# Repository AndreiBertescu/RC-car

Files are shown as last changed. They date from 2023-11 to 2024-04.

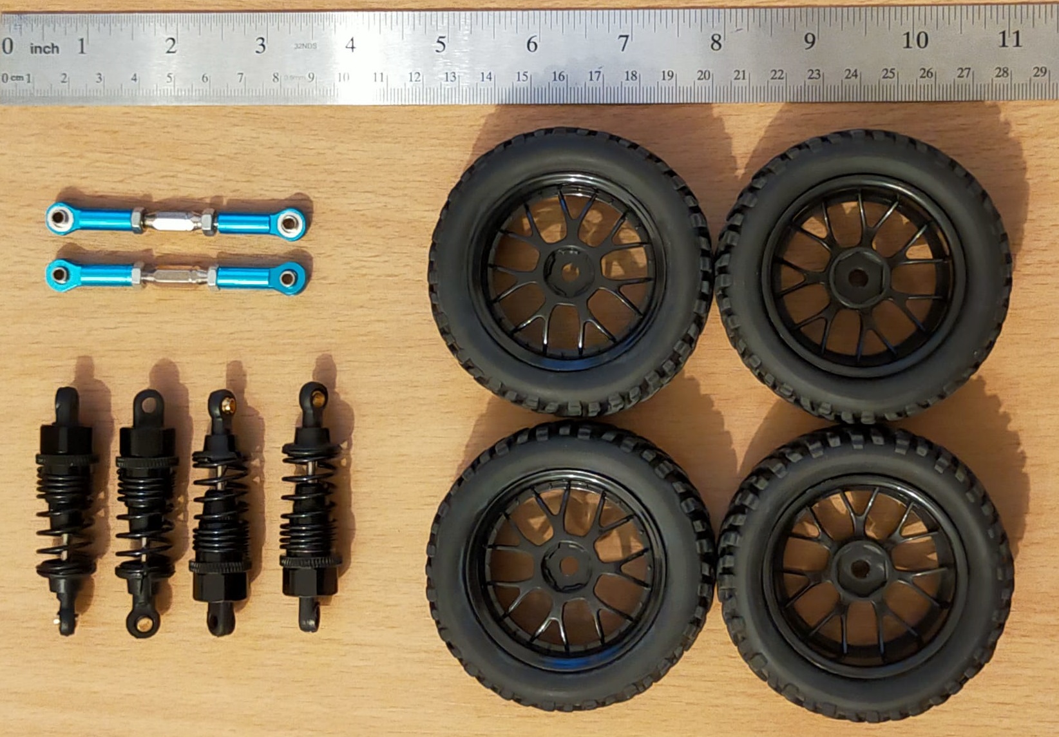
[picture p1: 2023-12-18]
Photos/Parts.jpg

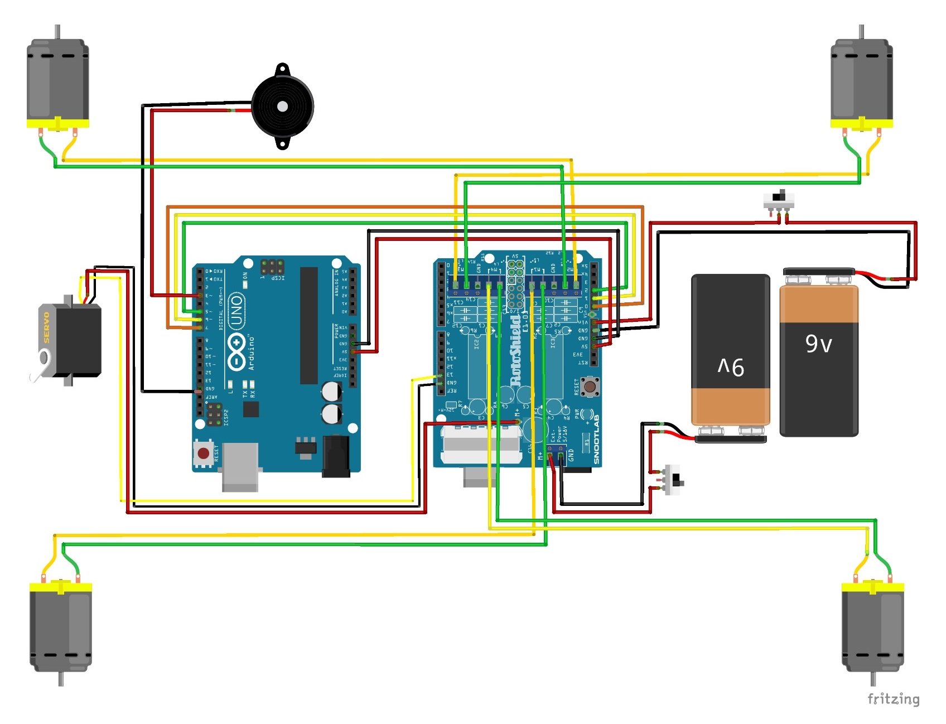
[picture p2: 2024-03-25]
Photos/Schematic.jpg

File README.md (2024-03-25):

# RC Car Project

This project aims to create an Arduino-controlled RC car.

<p align="center">
  
  
  
  
</p>

## Description

The setup includes a Plusivo Arduino Uno, paired with an Arduino WiFi board, and a quad H-bridge motor controller. To control the car, the WiFi board initiates a server, a WiFi access point and starts a RC-car-control web page. The car can be controlled from any device using the site's graphical user interface or by connecting any controller supported by the browser.

Two Arduino boards are used because the WiFi board lacks access to the OCR2A/B and OCR0A/B timers, while the Arduino Uno lacks built-in WiFi capability.

The car's chassis was designed in Fusion360 and will be 3D printed using PLA filament, while the wheels, suspensions, motors, battery, and wires are purchased separately. The car can work in two modes: one where the servo is not used to steer the car, only the wheels, and one where the servo is connected to the two steering axles, thus turning the wheels. In the former working mode, two stoppers have been designed to prevent the wheels from spinning on their own.

## Components
- 1x Arduino UNO R3 board: [datasheet](https://docs.arduino.cc/resources/datasheets/A000066-datasheet.pdf)
- 1x WEMOS ESP8266 D1 R2 board: [details](https://wiki.geekworm.com/WEMOS_ESP8266_D1_R2_V2.1)
- 1x L293D quad H-bridge motor controller shield: [manual](https://cdn-learn.adafruit.com/downloads/pdf/adafruit-motor-shield.pdf)
- 1x passive buzzer
- 4x 7.5cm diameter wheels.
- 4x 6cm hole-to-hole suspensions.
- 2x 6.5cm hole-to-hole steering axels (which have been extended).
- 1x MG996R 10Kg/cm servo motor for the steering arrangement.
- 2x 9V battery (which can be replaced with any rechargeable battery) - one for the motors and one for the control boards.
- A bunch of wires.
- Acces to a 3D-printer for the chassis.
- 
### Screws
- 8 x M3x20
- 20 x M4x15
- 12 x M4x40
- 16 x M5x30
- 16 x M5x40

## Controls for an Xbox controller
- Right joystick for steering
- Light joystick for speed
- Y button for START/STOP button
- B button for honk
- A button for steering lock

## Notes
- The joystick in the rc-car-control web page was made with the help of this tutorial: [link](https://www.instructables.com/Making-a-Joystick-With-HTML-pure-JavaScript/)
- The 'ArduinoWifiDriver' directory was included because of a recurring error when trying to write the program on the D1 R2 board.
- The website url to control the car is: http://192.168.4.1
- The website will load only if you are connected to the propper wifi network named '**RC-CAR_ESP8266**' with the password '**password**'.
- The Wheel-Connector model was not utilized. Instead, 4x M4x15 screws with a 2mm hole drilled in their center were used to connect the motors with the wheels.

## Version 1.4
- Added schematic
- Added passive buzzer with honk feature
- Added custom paintjob

## Version 1.3
- Updated chassis models with two available extensions: one specific to Fusion360 and stl.
- The total amount of filament used is 123 meters.

## Version 1.2
- Rechecked the Arduino Uno code to ensure it works
- Updated the README to include the schematic and part names

## Version 1.1
- Remade website to be more responsive
- Remade ArduinoWifi code to be more readable
- Removed the ability of the Arduino to connect to other wifi networks for simplicity

## Version 1.0
- Added project to GitHub

## Images
- Schematic
Schematic

- Car model


- Bought parts


- L293D motor controller


- WEMOS ESP8266 D1 R2


- Arduino UNO R3


- Front wheels assembly


- Small car components prepared for 3d-printing


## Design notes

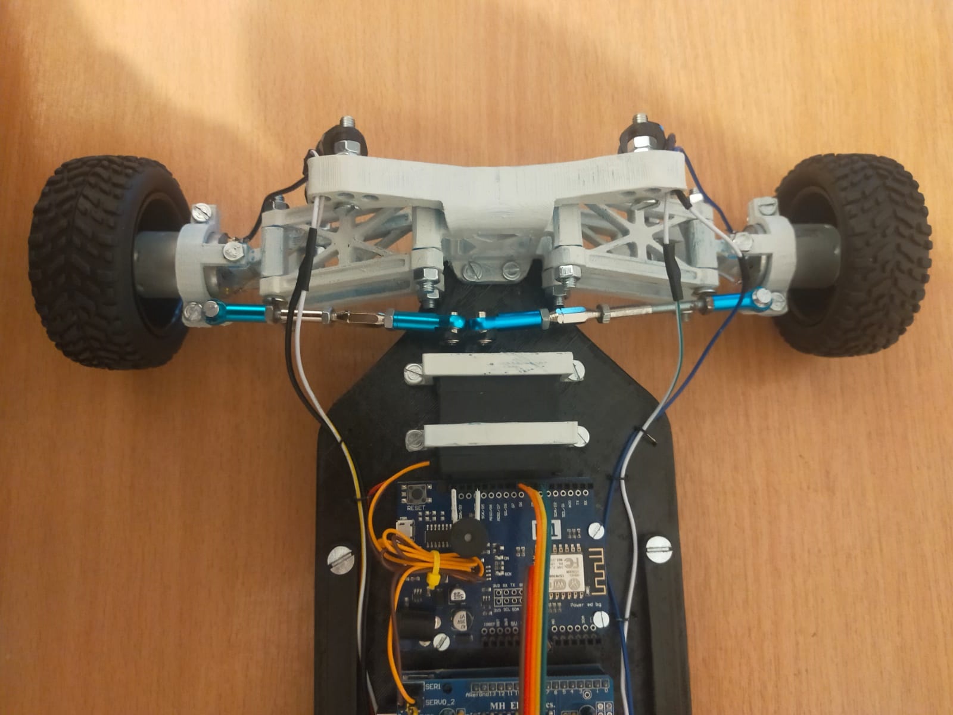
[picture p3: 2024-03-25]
Photos/Car1.jpg

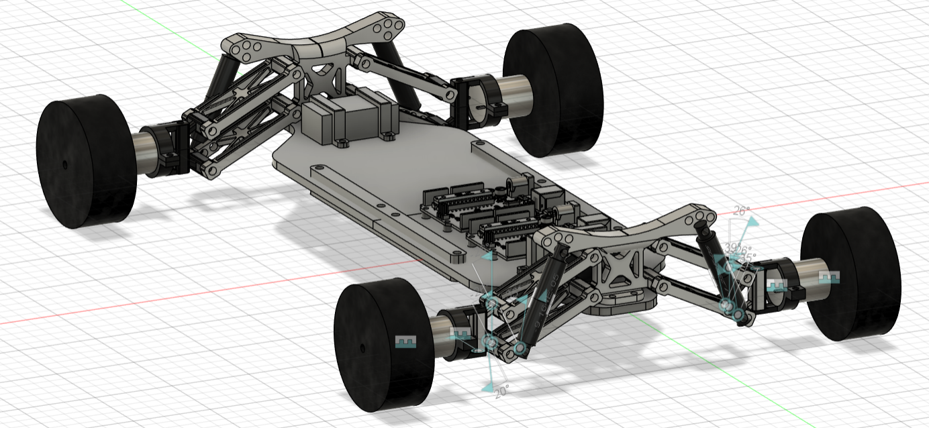
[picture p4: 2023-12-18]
Photos/Model3.png

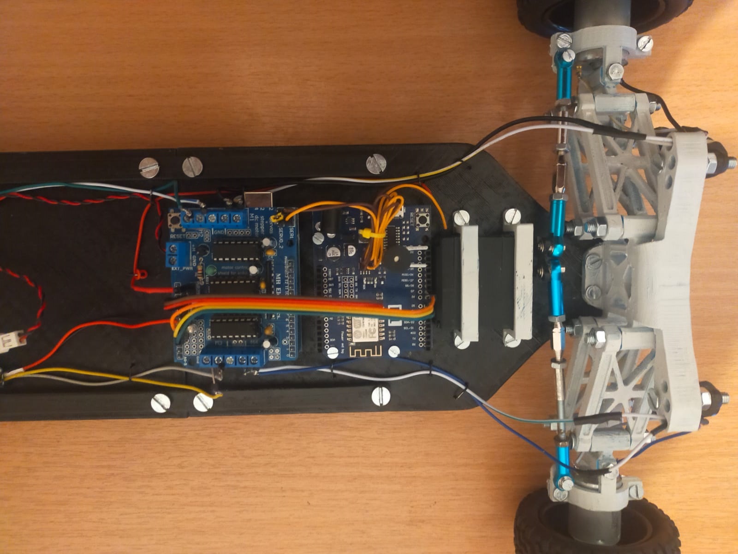
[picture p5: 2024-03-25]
Photos/Car4.jpg

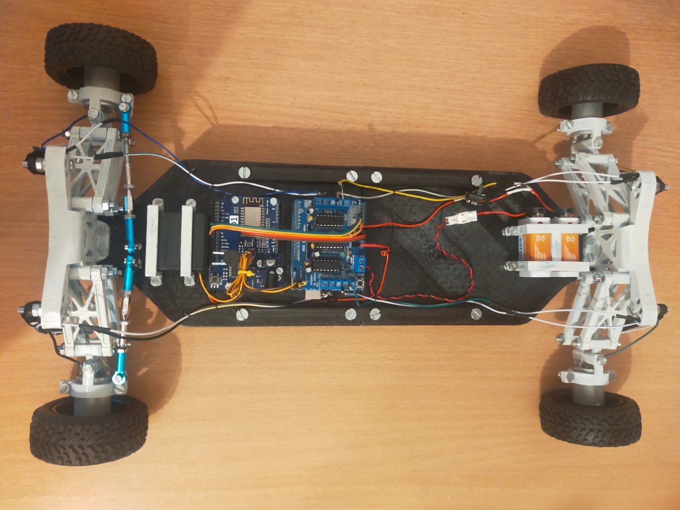
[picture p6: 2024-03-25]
Photos/Car2.jpg

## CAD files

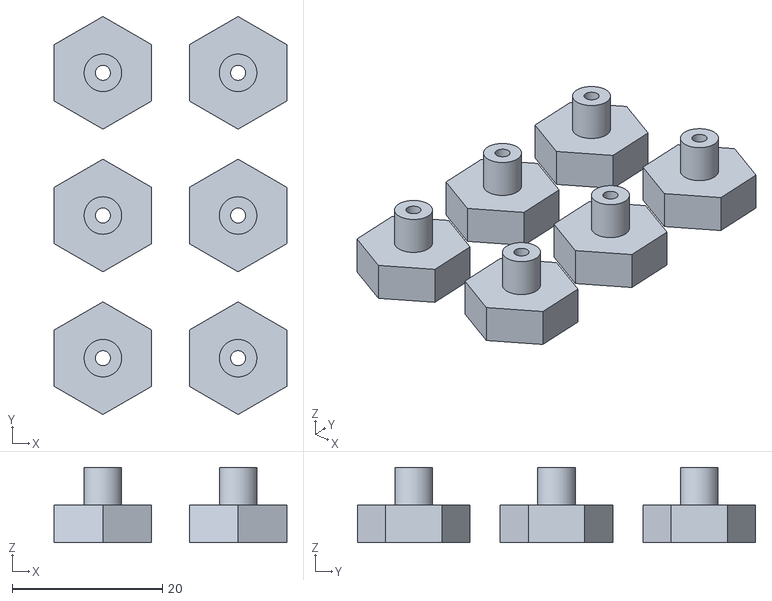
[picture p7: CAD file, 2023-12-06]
Model/Wheeel-Connectors.stl
31.0 x 53.0 x 10.0

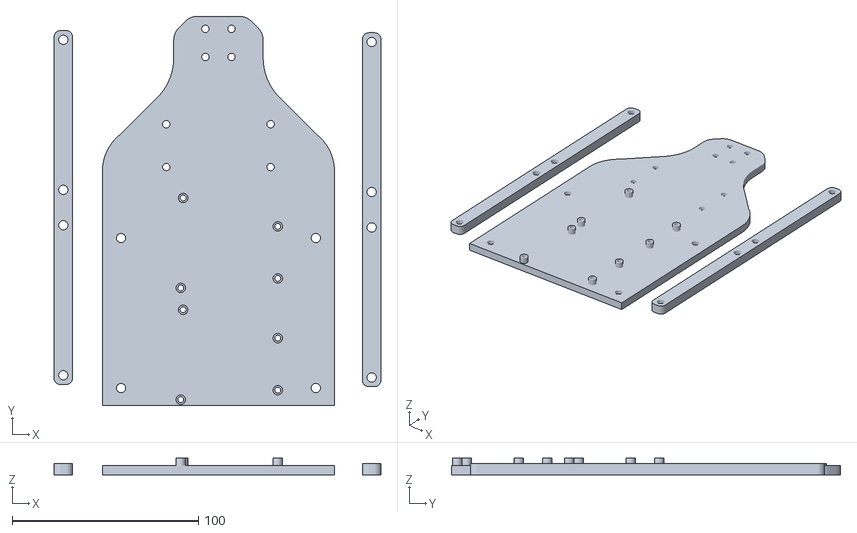
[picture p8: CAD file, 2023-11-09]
Model/3D-Plate1.stl
175.5 x 209.0 x 9.00

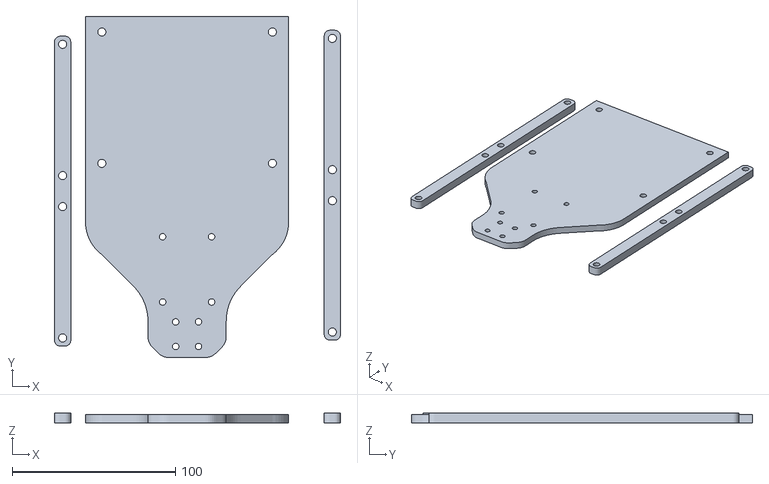
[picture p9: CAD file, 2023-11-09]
Model/3D-Plate2.stl
175.3 x 209.0 x 6.00

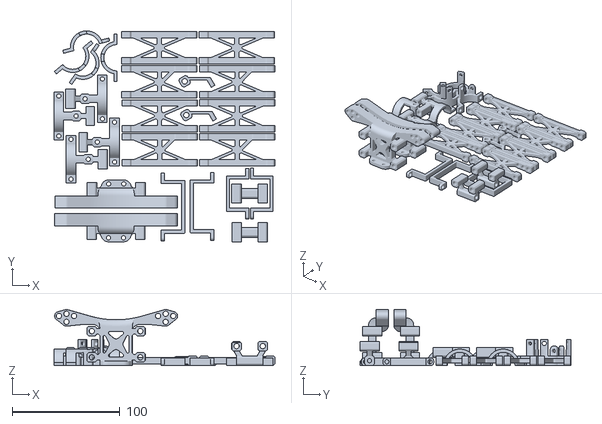
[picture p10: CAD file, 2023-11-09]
Model/3D-Components.stl
205.0 x 196.0 x 52.0

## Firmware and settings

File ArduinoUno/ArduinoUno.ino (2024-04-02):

#include <AFMotor.h>
#include <Servo.h>

AF_DCMotor motorForwardRight(2);
AF_DCMotor motorForwardLeft(3);
AF_DCMotor motorBackRight(1);
AF_DCMotor motorBackLeft(4);
int speed = 0;
int steering = 0;
bool steeringEnabled = 0;  //true when the servo is used

Servo steeringSero;  // create servo object to control a servo
int servoPos = 0;

//////////////////////SETTINGS
#define SPEED_PIN A2            //speed analog pin
#define STEERING_PIN A1         //steering analog pin
#define STEERING_ENABLE_PIN A0  //steering lock analog/digital pin
void setup() {
  Serial.begin(9600);

  pinMode(SPEED_PIN, INPUT);
  pinMode(STEERING_PIN, INPUT);
  pinMode(STEERING_ENABLE_PIN, INPUT);

  steeringSero.attach(10);
}

void loop() {
  retrieveValues();
  handleMotors();

  printValues();
  // printValueTimings();
}

void printValues() {
  Serial.print(speed);
  Serial.print(" ");
  Serial.print(steering);
  Serial.print(" ");
  Serial.print(steeringEnabled);
  Serial.println();
  delay(100);
}

void printValueTimings() {
  Serial.print(pulseIn(SPEED_PIN, HIGH, 980000));
  Serial.print(" ");
  Serial.print(pulseIn(STEERING_PIN, HIGH, 980000));
  Serial.print(" ");
  Serial.print(digitalRead(STEERING_ENABLE_PIN));
  Serial.println();
  delay(100);
}

void retrieveValues() {
  speed = map(pulseIn(SPEED_PIN, HIGH, 980000), 20, 975, -255, 255);
  steering = map(pulseIn(STEERING_PIN, HIGH, 980000), 20, 975, -255, 255);
  speed = (abs(speed) < 1 || abs(speed) >= 256) ? 0 : speed / 10 * 10;
  steering = (abs(steering) < 1 || abs(steering) >= 256) ? 0 : steering / 10 * 10;
  steeringEnabled = digitalRead(STEERING_ENABLE_PIN);
}

void handleMotors() {
  motorForwardRight.setSpeed(abs(speed));
  motorForwardLeft.setSpeed(abs(speed));
  motorBackRight.setSpeed(abs(speed));
  motorBackLeft.setSpeed(abs(speed));

  if (abs(speed) < 100) {
    motorForwardRight.run(RELEASE);
    motorForwardLeft.run(RELEASE);
    motorBackRight.run(RELEASE);
    motorBackLeft.run(RELEASE);
  } else if (speed >= 100) {
    motorForwardRight.run(FORWARD);
    motorForwardLeft.run(FORWARD);
    motorBackRight.run(FORWARD);
    motorBackLeft.run(FORWARD);
  } else if (speed <= -100) {
    motorForwardRight.run(BACKWARD);
    motorForwardLeft.run(BACKWARD);
    motorBackRight.run(BACKWARD);
    motorBackLeft.run(BACKWARD);
  }

  if (steeringEnabled) {
    if (abs(steering) > 50)
      steeringSero.write(map(steering, -255, 255, 135, 45));
    else
      steeringSero.write(90);
  } else if(abs(steering) > 100 && abs(speed) < 100){
    motorForwardRight.setSpeed(abs(steering));
    motorForwardLeft.setSpeed(abs(steering));
    motorBackRight.setSpeed(abs(steering));
    motorBackLeft.setSpeed(abs(steering));

    if (steering <= -100) {
      motorForwardRight.run(BACKWARD);
      motorForwardLeft.run(FORWARD);
      motorBackRight.run(BACKWARD);
      motorBackLeft.run(FORWARD);
    } else if (steering >= 100) {
      motorForwardRight.run(FORWARD);
      motorForwardLeft.run(BACKWARD);
      motorBackRight.run(FORWARD);
      motorBackLeft.run(BACKWARD);
    }
  }
}

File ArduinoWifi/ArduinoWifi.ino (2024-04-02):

#include <ESP8266WiFi.h>
#include <ESP8266WebServer.h>

ESP8266WebServer server(80);

int speed = 0;
int steering = 0;
bool stop = false;
bool steeringLock = false;
bool honk = false;

extern const char mainPage[] PROGMEM;
const char *ssid = "RC-CAR_ESP8266";  //wi-fi network name
const char *password = "password";    //wi-fi password

///////////////SETTINGS
//The website url is: http://192.168.4.1
#define SPEED_PIN D5          //speed pin
#define STEERING_PIN D6       //steering pin
#define STEERING_LOCK_PIN D7  //steering lock pin
#define HONK_PIN D3           //honk pin

void setup() {
  pinMode(SPEED_PIN, OUTPUT);
  pinMode(STEERING_PIN, OUTPUT);
  pinMode(STEERING_LOCK_PIN, OUTPUT);
  pinMode(HONK_PIN, OUTPUT);

  Serial.begin(9600);
  delay(100);

  startServer();
}

void loop() {
  server.handleClient();

  if (stop == 1) {
    speed = 0;
    steering = 0;
  }

  analogWrite(SPEED_PIN, (int)map(speed, -125, 125, 5, 250));
  analogWrite(STEERING_PIN, (int)map(steering, -125, 125, 5, 250));
  analogWrite(STEERING_LOCK_PIN, steeringLock ? 250 : 5);

  if (honk)
    tone(HONK_PIN, 1000);
  else
    noTone(HONK_PIN);

  // printData();
}

void printData() {
  Serial.print(stop);
  Serial.print(" ");
  Serial.print(speed);
  Serial.print(" ");
  Serial.print(steering);
  Serial.print(" ");
  Serial.print(steeringLock);
  Serial.print(" ");
  Serial.println(honk);
}

void startServer() {
  WiFi.softAP(ssid, password);

  server.on("/", HTTP_GET, handleRoot);

  server.on("/data", HTTP_POST, handleData);

  server.onNotFound([]() {
    server.send(404, "text/plain", "404: Not found");
  });

  server.begin();
  Serial.println("\nServer started");
}

void handleRoot() {
  server.send(200, "text/html", mainPage);
}

void handleData() {
  if (server.hasArg("data")) {
    int nr = 0, aux = 0;
    String data = server.arg("data");
    String packets[6];

    for (int i = 0; i < data.length(); i++)
      if (data.charAt(i) == ' ') {
        packets[nr++] = data.substring(aux, i);
        aux = i + 1;
      }
    packets[4] = data.substring(aux, data.length());

    stop = packets[0] == "1" ? true : false;
    speed = packets[1].toInt();
    steering = packets[2].toInt();
    steeringLock = packets[3] == "1" ? true : false;
    honk = packets[4] == "1" ? true : false;

    server.send(200, "text/plain", "Data received: " + data);
  } else {
    Serial.println("Data not recieved.");
    server.send(400, "text/plain", "Bad Request");
  }
}

////////////////Web Page
const char mainPage[] PROGMEM =
  R"=====(
<!DOCTYPE html>
<html lang="en">
<head>
<meta charset="UTF-8">
<meta name="viewport" content="width=device-width, initial-scale=1.0">
<meta http-equiv="X-UA-Compatible" content="ie=edge">
<title>RC Control Panel</title>
	
<style>
* {
  margin: 0;
  padding: 0;
  border-width: 0;
  text-align: center;
  color: #042940;
  font-family: -apple-system, BlinkMacSystemFont, "Segoe UI", Roboto, "Helvetica Neue", Arial, "Noto Sans", sans-serif, "Apple Color Emoji", "Segoe UI Emoji", "Segoe UI Symbol", "Noto Color Emoji";
  transition-duration: 0.2s;
  -webkit-touch-callout: none;
  -webkit-user-select: none;
  -khtml-user-select: none;
  -moz-user-select: none;
  -ms-user-select: none;
  user-select: none;
  font-weight: bold;
  overflow: hidden;
}
#mainContainer {
  width: 100%;
  height: 100vh;
  background: #005C53;
  display: flex;
  justify-content: center;
  align-items: center;
}
#mainDiv {
  min-width: 40vw;
  height: 100vh;
  background: #9FC131;
  border-radius: 3px;
  padding: 10px 0;
}
.paragraph {
  font-size: 18px;
  display: flex;
  justify-content: center;
  align-items: center;
  padding: 2%;
  min-height: 30px;
}
.paragraphRight {
  padding: 10%;
}
.dot {
  height: 25px;
  width: 25px;
  background-color: red;
  border: 2px solid #042940;
  border-radius: 30%;
  display: inline-block;
}
#sLock {
  margin-left: 10px;
  padding: 3% 6%;
  border-radius: 10px;
  border: 2px solid black;
  background: none;
  font-size: 18px;
}
#sLock:hover {
  background: rgba(0, 0, 0, 0.2);
}
#sLock:active {
  margin-left: 10px;
  padding: 3% 6%;
  background: rgba(0, 0, 0, 0.3);
}
#stop {
  font-size: 18px;
  padding: 5% 15%;
  border-radius: 5px;
  background: green;
  border: 3px solid #042940;
}
#honk {
  font-size: 18px;
  padding: 5% 5%;
  margin-right: 15px;
  border-radius: 5px;
  background: #0FB1BC;
  border: 3px solid #042940;
}
#honk:active {
  background: #0C919A;
}	
/* --------------------ProgressBars-------------------- */
#verticalBarContainer {
  position: relative;
  background-color: #9BC9C7;
  width: 50px;
  max-width: 100%;
  height: 80%;
  margin-left: calc(50% - 25px);
  margin-bottom: 5px;
}
#verticalBar {
  position: absolute;
  background-color: #199c85;
  bottom: 50%;
  width: 100%;
  height: 0px;
  transition-duration: 0s;
}
#horizontalBarContainer {
  position: relative;
  background-color: #9BC9C7;
  width: 80%;
  margin-left: 10%;
  height: 50px;
}
#horizontalBar {
  position: absolute;
  background-color: #199c85;
  left: 50%;
  width: 0px;
  height: 100%;
  transition-duration: 0s;
}
/* --------------------/ProgressBars-------------------- */
@media screen and (max-width: 900px) {
	#mainDiv {
	  min-width: 70vw;
	}
	#mainTitle{
		display: none;
	}
}
@media screen and (max-width: 600px) {
	#mainDiv {
	  min-width: 100vw;
	}
	#mainTitle{
		display: none;
	}
}
</style>
</head>
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

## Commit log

2023-11-09 Version 1.3
    [3D-Components.stl, 3D-Plate1.stl, 3D-Plate2.stl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]
2023-12-06 Added Wheel-Connectors model
    [Wheeel-Connectors.stl, Wheel-Connectors.f3d]
2024-02-18 Changed steering code on ArduinoUno.ino
2024-02-25 Changed ArduinoUno.ino code and updated photos
    [Wheel-Connectors.f3d]
